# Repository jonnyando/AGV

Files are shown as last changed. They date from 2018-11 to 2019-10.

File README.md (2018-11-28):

# AGV

##Current Specs
- BLDC motor driver
- STM32F103C8 microcontroller
- LEDs on each phase's PWM output, so they will breath in sync with the speed of the motor
- Sense lines on all three phases, allowing sensorless operation
- UART connector
- SWD connector
- Vin up to 24V (need to double check voltage range on all parts)
- 3.3v linear reg (want to replace with switched)
- 3.3v rail indicator LED
- four quadrant operation (sw not yet implemented)

## TO DO
- add connection for rotary encoder
- add silkscreen indication for power input
- add bulk input capacitance
- get overall size down a little
- determine if parallel 'FETs are necessary for desired use cases.
- determine power handling capability (similar to above)

- usb port? depends on uC. Would need isolation probably
- isolated uart/i2c/spi port, for receiving commands from master/host
- add adc?

## Fixes:
- add power led on VBUS
- add led to EN_GATE pin to tell state
- increase drill size on stitching vias (currently unnecessarily small)
- fix/remove thermal relief on source pads for left most FETs
- add method to sense line voltages on each output phase, for back EMF sensing
- add fourth mounting hole
- increase package size where applicable (0402s are unnecessarily small in some places)
- do the capacitors on the back need to be there? maybe align them better at least
- improve fill polygon around C5 and C6
- align power leds more appropriately

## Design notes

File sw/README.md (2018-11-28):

# Software

to setup toolchain, download latest [arm-non-eabi-gcc package](https://developer.arm.com/open-source/gnu-toolchain/gnu-rm/downloads)

```bash
$ cd "${HOME}"/opt
$ tar xjf ~/Downloads/gcc-arm-none-eabi-7-2017-q4-major-linux.tar.bz2
$ chmod -R -w "${HOME}"/opt/gcc-arm-none-eabi-7-2017-q4-major
```

Update Makefile with __BINPATH__ reflecting the */opt/gcc-arm-none-eabi-7-2017-q4-major/bin/* folder created

vscode:
visual theme : `atom one dark`
icon theme : `material icon theme`

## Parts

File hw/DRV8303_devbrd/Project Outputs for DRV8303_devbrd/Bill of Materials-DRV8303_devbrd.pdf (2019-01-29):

Comment | Description | Designator | Footprint | LibRef | Quan tity
0.022uF | Non polarized capacitor | C1 | RESC0603(1608)_N | Capacitor | 1
1uF | Non polarized capacitor | C2, C3, C15, C24, C25 | RESC0603(1608)_N | Capacitor | 5
2.2uF | Non polarized capacitor | C4 | RESC0603(1608)_N | Capacitor | 1
4.7uF | Non polarized capacitor | C5 | RESC0603(1608)_N | Capacitor | 1
0.1uF | Non polarized capacitor | C6, C7, C8, C9, C10, C11, C21, C22, C23 | RESC0603(1608)_N | Capacitor | 9
2200pF | Non polarized capacitor | C12, C13 | RESC0603(1608)_N | Capacitor | 2
100nF | Non polarized capacitor | C14, C16, C17, C18, C20 | RESC0603(1608)_N | Capacitor | 5
10uF | Non polarized capacitor | C19 | RESC0603(1608)_N | Capacitor | 1
LED | | D1, D2, D3, D4, D5, D9 | 0603 | LED | 6
Diode_schottky | | D6, D7, D8 | SOD523 | Diode_schottky | 3
Mounting_hole | | M1, M2, M3, M4 | M3_drill | Mounting_hole | 4
Header 6 | Header, 6-Pin | P1 | HDR1X6 | Header 6 | 1
Header 4 | Header, 4-Pin | P2 | HDR1X4 | Header 4 | 1
ScrewTerm_2 | | P3 | ScrewTerm_2 | ScrewTerm_2 | 1
ScrewTerm_3 | | P4 | ScrewTerm_3 | ScrewTerm_3 | 1
FDMS7682 | | Q1, Q2, Q3, Q4, Q5, Q6, Q7, Q8, Q9, Q10, Q11, Q12 | PQFN8_5x6 | FDMS7682 | 12
0R | Resistor | R1 | RESC0603(1608)_N | Resistor | 1
10R | Resistor | R2, R3, R5, R6, R8, R9 | RESC0603(1608)_N | Resistor | 6
0.01R | Resistor | R4, R7 | RESC1206(3216)_M | Resistor | 2
56R | Resistor | R10, R11 | RESC0603(1608)_N | Resistor | 2
10KR | Resistor | R12, R13, R23, R24, R25 | RESC0603(1608)_N | Resistor | 5
1KR | Resistor | R14, R15, R16, R17, R18, R19, R29 | RESC0603(1608)_N | Resistor | 7
68KR | Resistor | R20, R21, R22 | RESC0603(1608)_N | Resistor | 3
DRV8303 | | U1 | HSSOP48 | DRV8303 | 1
STM32F103C8T6 | ARM Cortex-M3 32-bit MCU, 64 KB Flash, 20 KB Internal RAM, 37 I/Os, 48-pin LQFP, -40 to 85 degC, Tray | U2 | STM-LQFP48_N | STM32F103C8T 6 | 1
AZ1117EH | | U3 | SOT-223 | AZ1117EH | 1

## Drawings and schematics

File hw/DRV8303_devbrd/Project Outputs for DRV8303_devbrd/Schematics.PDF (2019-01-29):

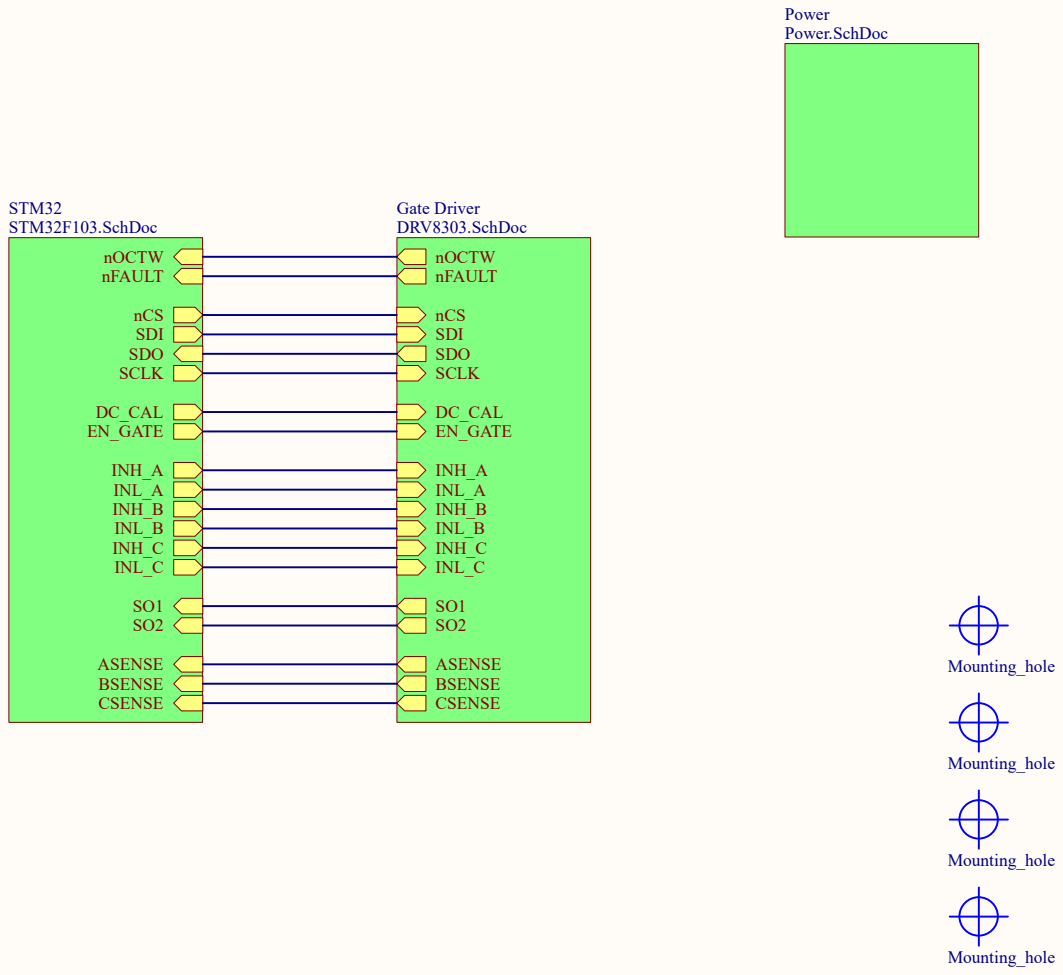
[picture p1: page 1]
Title; Size; Number; Revision; Date:; Sheet; File:; C:\Users\..\TopLevel.SchDoc; Drawn By:; nOCTW; nCS SDI; nFAULT; SDO SCLK; DC_CAL EN_GATE; INH_A INL_A INH_B INL_B INH_C INL_C; ASENSE BSENSE CSENSE; STM32 STM32F103.SchDoc; CSENSE; ASENSE BSENSE; Gate Driver DRV8303.SchDoc; Power Power.SchDoc; Mounting_hole

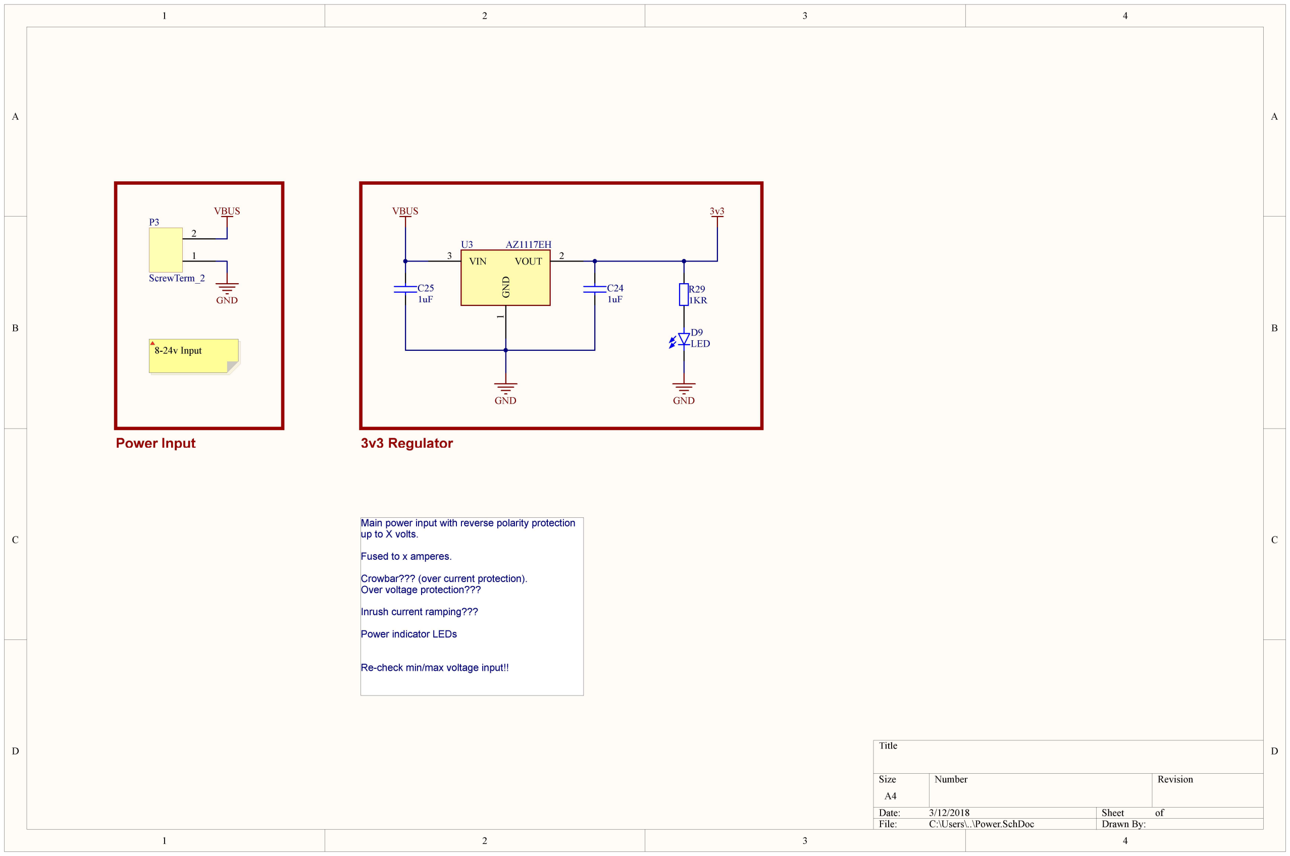
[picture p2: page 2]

D D

C C

B B

A A

Title

Size | Number | Revision
A4
File: | C:\Users\..\Power.SchDoc | Drawn By:

Main power input with reverse polarity protection up to X volts.

Fused to x amperes.

Crowbar??? (over current protection). Over voltage protection???

Inrush current ramping???

Power indicator LEDs

Re-check min/max voltage input!!

1

2

P3

ScrewTerm_2

VBUS

GND

3v3

GND

VBUS

C25
1uF

D9
LED

R29
1KR

GND

Power Input | 3v3 Regulator | GND

1

VOUT | 2 VIN 3
U3 | AZ1117EH

C24
1uF

8-24v Input

GND | 46 GND | 47 GND | 48 GND

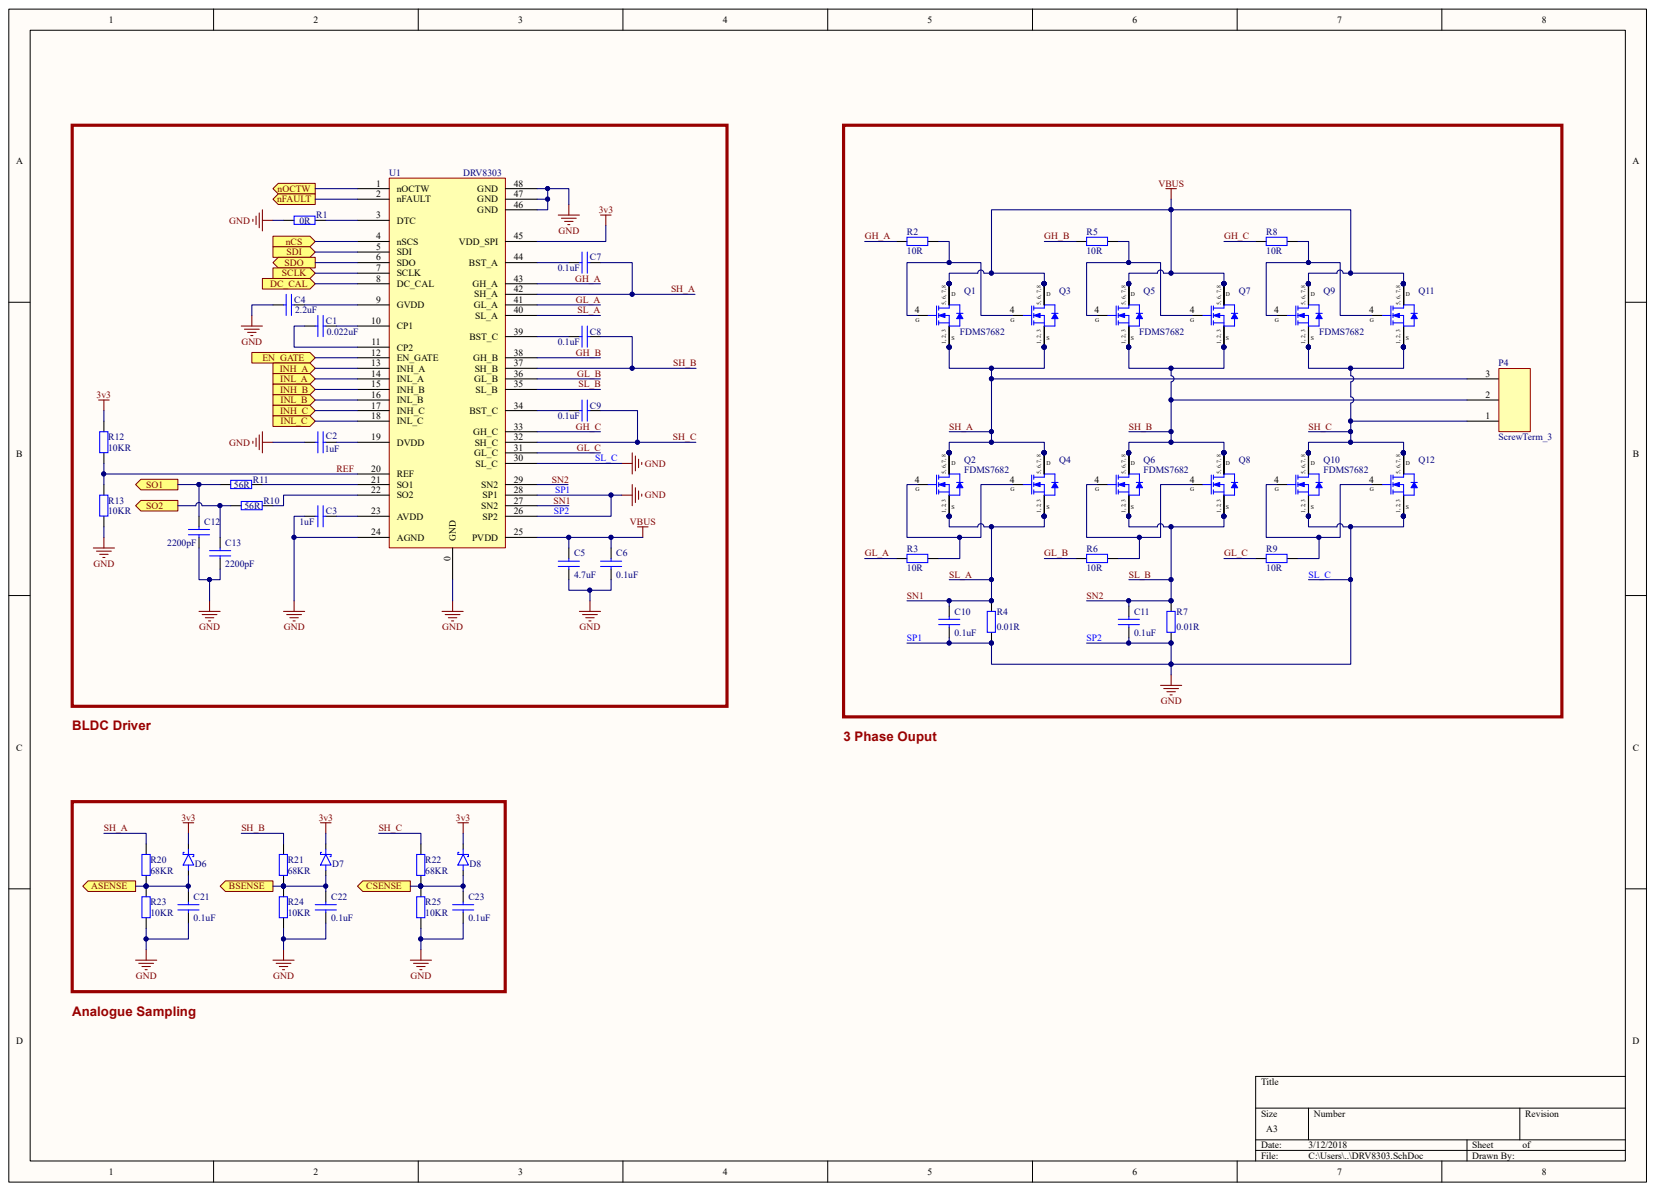
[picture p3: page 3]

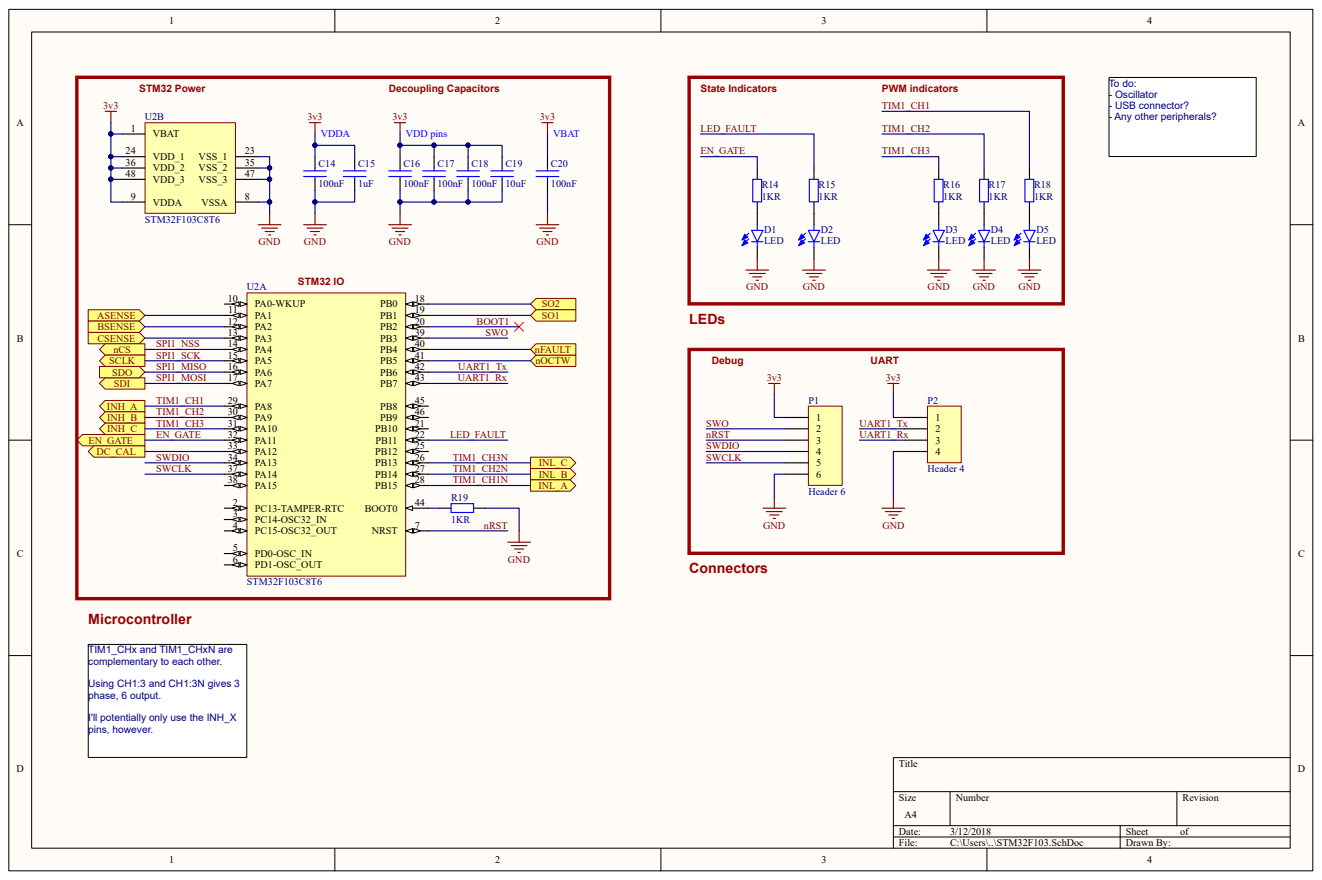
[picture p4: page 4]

TIM1_CHx and TIM1_CHxN are
complementary to each other.

I'll potentially only use the INH_X
pins, however.

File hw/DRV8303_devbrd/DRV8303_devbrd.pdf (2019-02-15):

Title; Size; Number; Revision; Date:; Sheet; File:; C:\Users\..\TopLevel.SchDoc; Drawn By:; nOCTW; nCS SDI; nFAULT; SDO SCLK; DC_CAL EN_GATE; INH_A INL_A INH_B INL_B INH_C INL_C; ASENSE BSENSE CSENSE; STM32 STM32F103.SchDoc; CSENSE; ASENSE BSENSE; Gate Driver DRV8303.SchDoc; Power Power.SchDoc; Mounting_hole

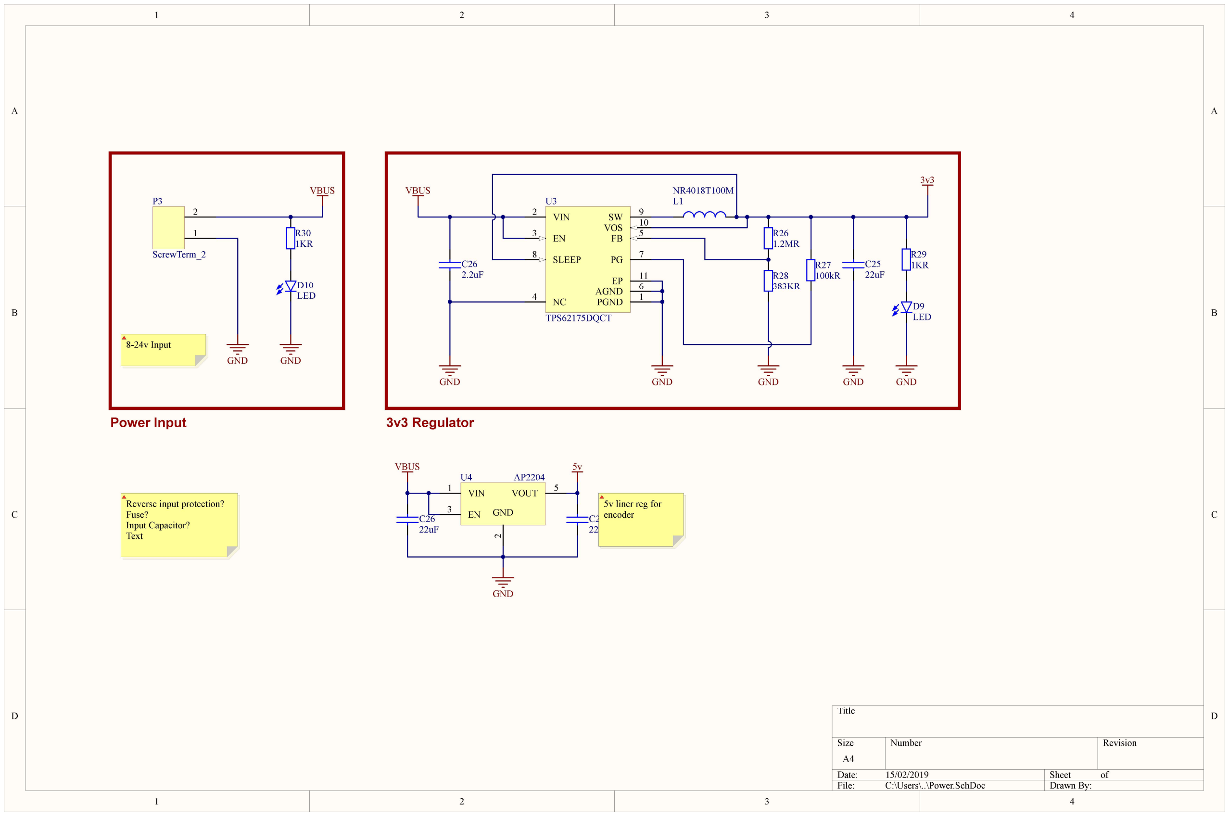
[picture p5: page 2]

D D

C C

B B

A A

Title

Size | Number | Revision
A4
File: | C:\Users\..\Power.SchDoc | Drawn By:

1

2

P3

ScrewTerm_2

VBUS

GND

D9
LED

R29
1KR

GND

Power Input | 3v3 Regulator
PGND | 1

VIN 2

EN 3

NC 4

FB | 5
AGND | 6
PG | 7 SLEEP 8
SW | 9
VOS | 10
EP | 11

U3

TPS62175DQCT

R26
1.2MR

R28
383KR

GND

C25
22uF

R27
100kR

GND

C26
2.2uF

VBUS

GND | GND

3v3

D10
LED

R30
1KR

GND

L1

NR4018T100M

GND

5v

VIN 1

GND2

EN 3

VOUT | 5
U4 | AP2204

VBUS

C26
22uF

C27
22uF

8-24v Input

Reverse input protection?
Fuse?
Input Capacitor?
Text

5v liner reg for
encoder

GND | 46 GND | 47 GND | 48 GND

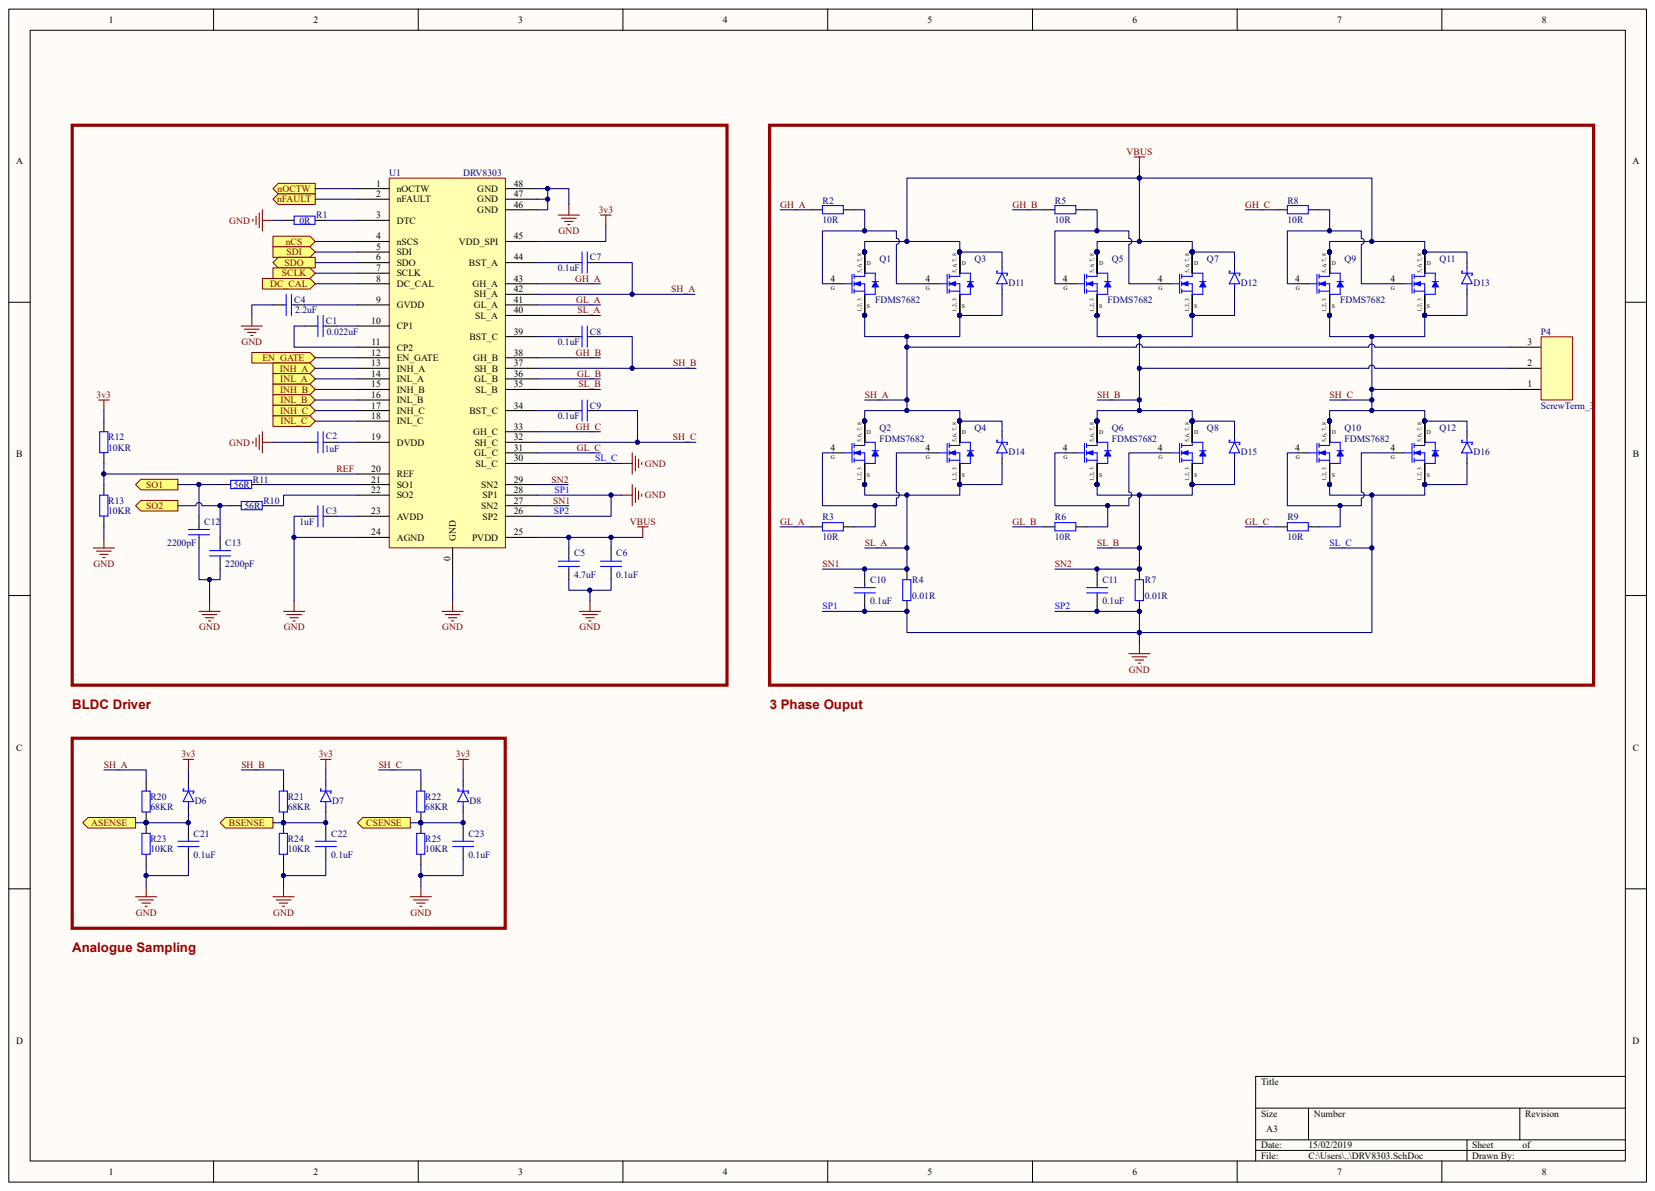
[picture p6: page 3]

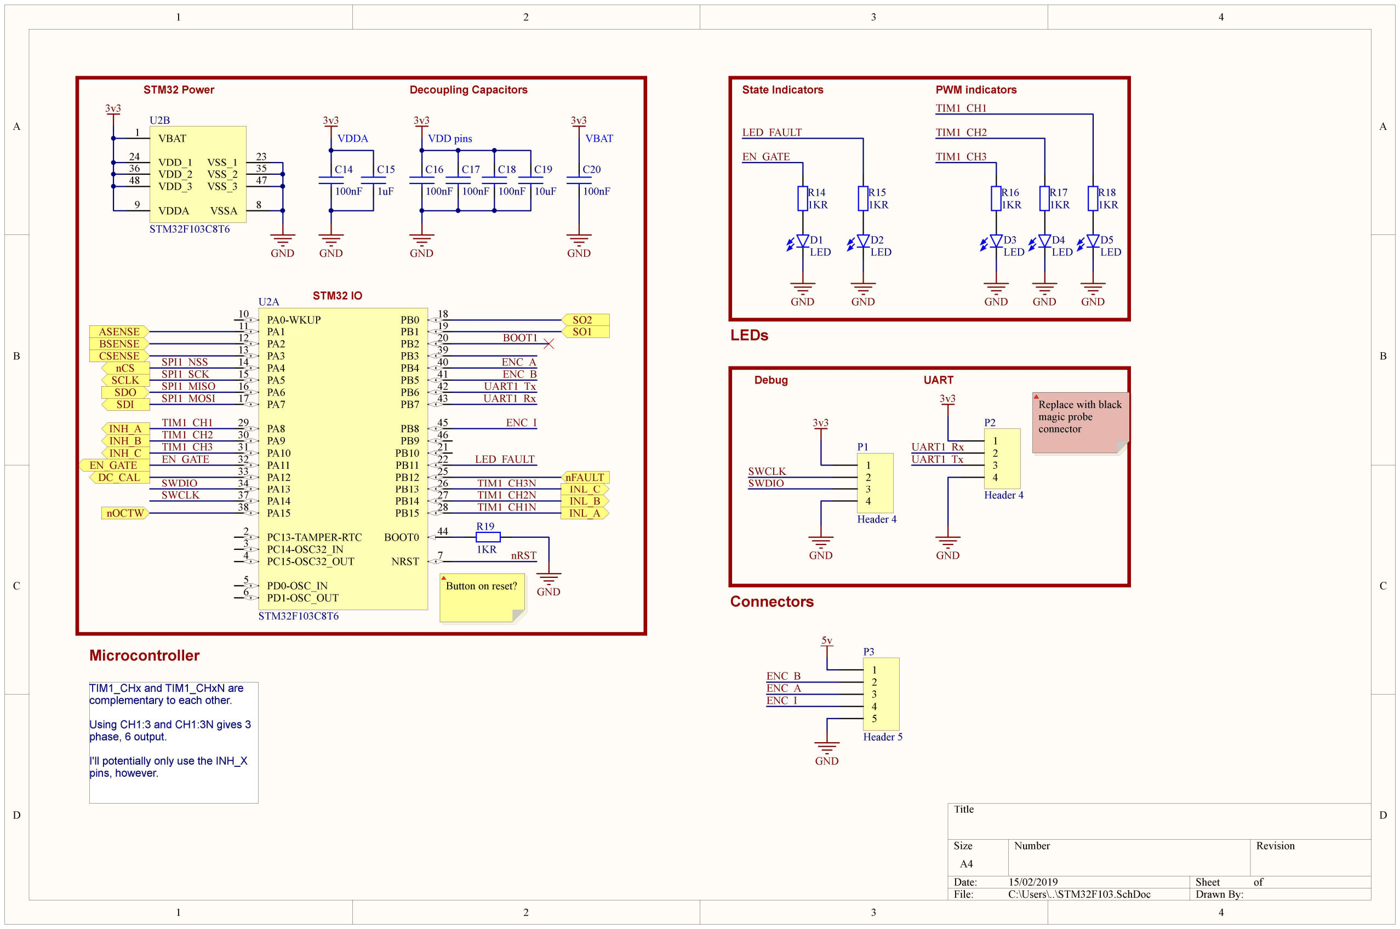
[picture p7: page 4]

D D

C C

B B

A A

Title

Size | Number | Revision
A4
File: | C:\Users\..\STM32F103.SchDoc | Drawn By:
BOOT0 | 44
NRST | 7

PA0-WKUP 10
PA1 11

PA10 31
PA11 32
PA12 33
PA13 34
PA14 37
PA15 38

PA2 12
PA3 13
PA4 14
PA5 15
PA6 16
PA7 17

PA8 29
PA9 30
PB0 | 18
PB1 | 19
PB10 | 21
PB11 | 22
PB12 | 25
PB13 | 26
PB14 | 27
PB15 | 28
PB2 | 20
PB3 | 39
PB4 | 40
PB5 | 41
PB6 | 42
PB7 | 43
PB8 | 45
PB9 | 46

PC13-TAMPER-RTC 2
PC14-OSC32_IN 3
PC15-OSC32_OUT 4

PD0-OSC_IN 5
PD1-OSC_OUT 6

U2A

STM32F103C8T6

VBAT 1

VDD_1 24
VDD_2 36
VDD_3 48

VDDA 9

VSS_1 | 23
VSS_2 | 35
VSS_3 | 47
VSSA | 8

U2B

STM32F103C8T6

EN_GATE

INH_A
INH_B

INL_B

INH_C

DC_CAL

nOCTW

nFAULT

GND

3v3

SWDIO

SWCLK

1
2
3
4

P2

Header 4

3v3

GND

UART1_Rx
UART1_Tx

R19

1KR

GND

nRST

SPI1_NSS
SPI1_SCK
SPI1_MISO
SPI1_MOSI

SWCLK

SWDIO

TIM1_CH1
TIM1_CH2
TIM1_CH3

TIM1_CH2N

TIM1_CHx and TIM1_CHxN are complementary to each other.

Using CH1:3 and CH1:3N gives 3 phase, 6 output.

I'll potentially only use the INH_X pins, however.

C16

100nF

C17

100nF

C18

100nF

C14

100nF

C15

1uF

C20

100nF

GND | GND | GND
3v3 | 3v3 | 3v3

C19

10uF

VDDA | VDD pins | VBAT
| Decoupling Capacitors
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
EN_GATE

EN_GATE

LED_FAULT

LED_FAULT

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
TIM1_CH1

TIM1_CH2

TIM1_CH3

STM32 Power

STM32 IO

## Microcontroller

## LEDs

State Indicators | PWM indicators

## Connectors

Debug | UART

ASENSE
BSENSE
CSENSE

UART1_Rx

UART1_Tx
SDI

nCS
SCLK
SDO

INL_C
INL_A TIM1_CH1N

TIM1_CH3N

SO2
SO1 BOOT1

1
2
3
4
5

P3

Header 5

ENC_A
ENC_B

ENC_I

5v

GND

ENC_A

ENC_B

ENC_I

1
2
3
4

P1

Header 4

Replace with black
magic probe
connector

Button on reset?

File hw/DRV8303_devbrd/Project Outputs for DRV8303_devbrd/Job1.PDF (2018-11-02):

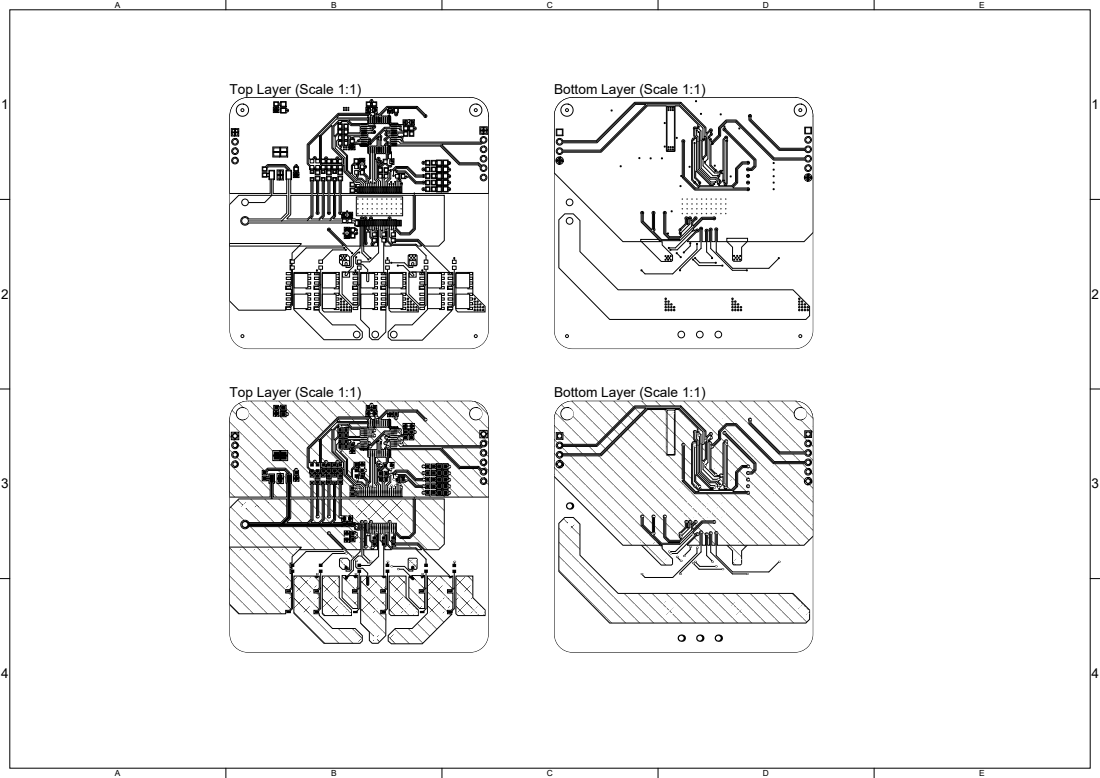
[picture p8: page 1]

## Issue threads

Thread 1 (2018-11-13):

Cannot communicate with DRV8303 over SPI

jonnyando, 2018-11-13:
Still debugging, but so far cannot see any data on the SDO line of the bus.

Current transmission looks like:
1. Lower chip select
2. transfer packet (R/W=1, address = 0010, data = 0)
3. Raise CS, delay 1mS, Lower CS
4. run SPI1_Tranceive(0x0000); to send zeroes and expecting to receive data back.

When running the above, only zeroes can be seen on the SDO line. No pulsing at all. Need to check IO configuration, but I expect it is correct.
Next things to check are baudrate, phase, and polarity of the clock.

jonnyando, 2018-11-14:
How it's initialised by ODrive firmware:
:   hspi3.Instance = SPI3;
   66:   hspi3.Init.Mode = SPI_MODE_MASTER;
   67:   hspi3.Init.Direction = SPI_DIRECTION_2LINES;
   68:   hspi3.Init.DataSize = SPI_DATASIZE_16BIT;
   69:   hspi3.Init.CLKPolarity = SPI_POLARITY_LOW;
   70:   hspi3.Init.CLKPhase = SPI_PHASE_2EDGE;
   71:   hspi3.Init.NSS = SPI_NSS_SOFT;
   72:   hspi3.Init.BaudRatePrescaler = SPI_BAUDRATEPRESCALER_16;
   73:   hspi3.Init.FirstBit = SPI_FIRSTBIT_MSB;
   74:   hspi3.Init.TIMode = SPI_TIMODE_DISABLE;
   75:   hspi3.Init.CRCCalculation = SPI_CRCCALCULATION_DISABLE;
   76:   hspi3.Init.CRCPolynomial = 10;

jonnyando, 2018-11-18:
Issue has been resolved.

There are two issues at play here - both hardware and software - with hardware being the biggest cause.

In the schematic, the placement of pins 23 and 24 are reversed, meaning AVDD is shorted directly to ground. Cutting the trace between that pin and the cap/via that bypasses it fixes the problem. The fix will be made in the schematic and new boards will be ordered soon.

For the software, I still haven't been able to figure out what hardware controlled NSS means, but I think it's only for Slave mode, so I've been using software controlled. The actual problem is the TX_empty flag gets raised before the transmission has completed on the hardware, so using that as a blocker to then raise chip select doesnt work and chip select get's raised about halfway through the transmission. I've implemented a NOP loop for the right amount of cycles, but will try to implement a proper delay function.

Closed 2018-11-18.

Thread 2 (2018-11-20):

PWM outputs are not connected to the correct pins

jonnyando, 2018-11-20:

jonnyando, 2018-12-27:
The pinout has been resolved in a new hardware revision, however PWM hasn't been implemented, so will no be determined if this is functioning until that time.

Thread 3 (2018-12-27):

inductive spiking kills 3.3v regulator

jonnyando, 2018-12-27:
On both boards with the 3v3 Reg, the regulator has shorted as soon as one of the motor phases is energised.

The output of the regulator is a direct short to ground. Checking the datasheet, the absolute maximum voltage input for the device is 16v. A spike of an extra 4v isn't crazy, so I believe when the motor phases' gates are raised, an inductive spike fries the regulator and kills the board.

I recommend implementing 2 fixes: input voltage clamping on the regulator and changing it to a switched-mode device.

One other "easier" alternative is to replace it with a 5v linear reg, which would presumably handle higher input voltages, but that's taking the easy way out.

jonnyando, 2019-05-20:
Added TVS in the latest hardware revision and have yet to see a similar failure.

Closed 2019-05-20.

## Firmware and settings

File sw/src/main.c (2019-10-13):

#include "main.h"

/* Private function prototypes -----------------------------------------------*/
void SystemClock_Config(void);

int __io_putchar(int ch)
{
    transmit_byte_uart(USART1, (uint8_t)ch);
    // ITM_SendChar(ch);
    return ch;
}

volatile uint32_t myTicks = 0;

void SysTick_Handler(void)
{
    myTicks++;
}

void DMA1_Channel1_IRQHandler(void){
    // pin_set(GPIOB, 11);
    if(DMA1->ISR & DMA_ISR_TEIF1){
        printf("DMA error\n");
        DMA1->IFCR |= (DMA_IFCR_CGIF1 | DMA_IFCR_CTEIF1);
    } else if(DMA1->ISR & DMA_ISR_HTIF1){
        // printf("DMA half transfer\n");
        DMA1->IFCR |= (DMA_IFCR_CGIF1 | DMA_IFCR_CHTIF1);
    } else if(DMA1->ISR & DMA_ISR_TCIF1){
        // printf("DMA transfer complete\n");
        DMA1->IFCR |= (DMA_IFCR_CGIF1 | DMA_IFCR_CTCIF1);
    }else if(DMA1->ISR & DMA_ISR_GIF1){
        // printf("DMA global interrupt\n");
        DMA1->IFCR |= DMA_IFCR_CGIF1;
    }
}

void ADC1_2_IRQHandler(void){
    // pin_set(GPIOB, 11);
    // blink_fault();
    // printf("ADC interrupt\n");
}

void HardFault_Handler(void){
    pin_set(GPIOB, 11);
}
void BusFault_Handler(void){
    pin_set(GPIOB, 11);
}
void UsageFault_Handler(void){
    pin_set(GPIOB, 11);
}

void myDelay(uint32_t mS){
    myTicks = 0;
    while(myTicks<mS);
}

uint16_t ADC_samples[10];

void blink_fault(void){
    pin_reset(GPIOB, 11);
    myDelay(50);
    pin_set(GPIOB, 11);
    myDelay(50);
    pin_reset(GPIOB, 11);
    myDelay(50);
    pin_set(GPIOB, 11);
}

int main(void)
{   
    // SystemInit();
    SystemClock_Config();



    pin_reset(GPIOB, 11);
    myDelay(50);
    pin_set(GPIOB, 11);
    myDelay(50);
    pin_reset(GPIOB, 11);
    myDelay(50);
    pin_set(GPIOB, 11);

    watchdog_set_prescaler(32);
    watchdog_set_reload_reg(0xfff);
    watchdog_start();

    GPIO_Init();
    UART_Init(USART1);
    UART_pin_Remap(USART1, 1);
    printf("uart1 initialized\n");
    printf("gpio initialized\n");
    SPI_Init(SPI1);             printf("SPI1 initialized\n");
    
    if(RCC->CSR & RCC_CSR_IWDGRSTF){
        printf("\nIWDG reset detected\n");
    }
    printf("mem adress: ADC1->DR=%d\n",&(ADC1->DR));
    

    NVIC_SetPriority(HardFault_IRQn, 0);
    NVIC_EnableIRQ(HardFault_IRQn);
    NVIC_SetPriority(BusFault_IRQn, 0);
    NVIC_EnableIRQ(BusFault_IRQn);
    NVIC_SetPriority(UsageFault_IRQn, 0);
    NVIC_EnableIRQ(UsageFault_IRQn);

    // printf("RCC->CR\t\t");          print_reg(RCC->CR,     32);

    RCC->AHBENR |= RCC_AHBENR_DMA1EN;
    DMA1_Channel1->CPAR = (uint32_t)&(ADC1->DR);
    DMA1_Channel1->CMAR = (uint32_t)ADC_samples;
    DMA1_Channel1->CNDTR = 5;
    DMA1_Channel1->CCR &= ~(DMA_CCR_PL_0 | DMA_CCR_PL_1);
    // DMA1_Channel1->CNDTR = (sizeof(ADC_samples)/sizeof(ADC_samples[0]));
    // memory icnrement
    // circular mode
    // set peripheral and memory sizes to 16b
    DMA1_Channel1->CCR |= DMA_CCR_MINC | DMA_CCR_CIRC 
                        | DMA_CCR_PSIZE_0 | DMA_CCR_MSIZE_0
                        | DMA_CCR_TEIE | DMA_CCR_TCIE | DMA_CCR_HTIE;
    // DMA1_Channel1->CCR &= ~(DMA_CCR_HTIE);
    DMA1_Channel1->CCR |= DMA_CCR_EN;
    
    // enable
    myDelay(500);

    printf("DMA1 Channel1 initialised\n");
    
    ADC1_Init();    printf("ADC1 initialized\n");

    ADC1->CR1 |= ADC_CR1_EOCIE;
    ADC1->CR2 |= ADC_CR2_CONT;
    ADC1->CR2 |= ADC_CR2_ADON;
    myDelay(10);
    ADC1->CR2 |= (ADC_CR2_RSTCAL);
    ADC1->CR2 |= (ADC_CR2_CAL);
    printf("adc on, calibrating...\n");
    while((ADC1->CR2) & (ADC_CR2_CAL)){
        // myDelay(1);
        ;
    }
    ADC1->CR2 |= ADC_CR2_ADON;


    myDelay(10);
    // print_reg(ADC1->CR2, 32);
    printf("adc on and calibrated\n");
    myDelay(10);
    myDelay(500);
    

    TIM1_Init();                printf("tim1 initialized\n");
    pin_reset(DC_CAL_Port, DC_CAL_Pin);
    printf("DC_CAL set LOW (off)\n");
    myDelay(10);
    uint16_t tx;
    uint16_t rx;

    drv8303_TypeDef drv;
    drv8303_Init(&drv, SPI1);
    drv_update(&drv);

    // sets OC_ADJ_SET to 24 (Vds = 1.043v)
    // Disable OCP
    // sets drv to 3-PWM mode
    // uint16_t set_reg = 0b01000000000 | 0b00000110000 | 0b00000001000;
    // uint16_t set_reg = (CR1_OC_ADJ_SET_24 | CR1_OCP_MODE_DISABLED | CR1_PWM_MODE_3);
    uint16_t set_reg = (CR1_OC_ADJ_SET_7 | CR1_PWM_MODE_3);
    pin_set(EN_GATE_Port, EN_GATE_Pin);
    myDelay(100);
    drv_write(&drv, DRV_CTRL_1, set_reg);
    printf("\nEnabled DRV8303\n");

    // myDelay(10);
    myDelay(500);
    printf("transmitting to drv\n");
    rx = drv_read(&drv, DRV_STATUS_1);
    printf("Status register 1\t");   print_reg(rx, 16);
    rx = drv_read(&drv, DRV_STATUS_2);
    printf("Status register 2\t");   print_reg(rx, 16);
    rx = drv_read(&drv, DRV_CTRL_1);
    printf("Control register 1\t");  print_reg(rx, 16);
    rx = drv_read(&drv, DRV_CTRL_2);
    printf("Control register 2\t");  print_reg(rx, 16);
    myDelay(10);
    // rx = drv_read(0x03);
    // printf("Control register 2\t");  print_reg(rx, 16);
    // myDelay(10);

    printf("\n");
    uint16_t t_del = 50;
    TIM1_enable();


    uint32_t angle_a = 0;
    uint32_t angle_b = 0;
    uint32_t angle_c = 0;
    uint32_t max_duty_cycle = 7500;
    uint16_t duty_cycle_a;
    uint16_t duty_cycle_b;
    uint16_t duty_cycle_c;
    uint16_t angle_step = 30;
    
    // uint8_t tc[3] = "abc";
    // transmit_byte_uart1(*tc);
    // transmit_byte_uart1('\n');
    // transmit_uart(USART1, tc, 3);

    drv_update(&drv);
    
    // drv_write(&drv, DRV_CTRL_1, set_reg);
    watchdog_reload();
    printf("Interrupts enabled\n");

    
    NVIC_SetPriority(DMA1_Channel1_IRQn, 1);
    NVIC_EnableIRQ(DMA1_Channel1_IRQn);
    NVIC_SetPriority(ADC1_IRQn, 2);
    NVIC_EnableIRQ(ADC1_IRQn);
    printf("while(1)\n");
    while (1){
        // while(1){
        //     ;
        // }
        // myDelay(200);
        // printf("beep..\n");
        // fflush(stdout);
        // ASENSE, BSENSE, CSENSE, A_CURR, B_CURR
        // for(int i = 0; i < 4; i++){
        //     printf("%d, ", ADC_samples[i]);
        // }
        // printf("%d\n", ADC_samples[4]);
        
        // if (DMA1->ISR & DMA_ISR_TEIF1){
        //     printf("DMA1 error interrupt\n");
        //     DMA1->IFCR |= DMA_IFCR_CTEIF1;
        //     DMA1->IFCR |= DMA_IFCR_CGIF1;
        // }
        // if (DMA1->ISR & DMA_ISR_HTIF1){
        //     printf("DMA1 half transfer interrupt\n");
        //     DMA1->IFCR |= DMA_IFCR_CHTIF1;
        //     DMA1->IFCR |= DMA_IFCR_CGIF1;
        // }
        // if (DMA1->ISR & DMA_ISR_TCIF1){
        //     printf("DMA1 transfer complete interrupt\n");
        //     DMA1->IFCR |= DMA_IFCR_CTCIF1;
        //     DMA1->IFCR |= DMA_IFCR_CGIF1;
        // }

        myDelay(10);

        // if(!pin_read(nOCTW_Port, nOCTW_Pin)){
        //     printf("nOCTW is LOW\n");
        //     pin_set(LED_FAULT_Port, LED_FAULT_Pin);
        // } else if(!pin_read(LED_FAULT_Port, nFAULT_Pin)){
        //     printf("nFAULT is LOW\n");
        //     pin_set(LED_FAULT_Port, LED_FAULT_Pin);
        // } else {
        //     pin_reset(LED_FAULT_Port, LED_FAULT_Pin);
        // }

        pin_reset(LED_FAULT_Port, LED_FAULT_Pin);

        angle_b = angle_a + 120;
        angle_c = angle_a + 240;

        duty_cycle_a = ((sin(angle_a * (PI/180))+1)/2)*max_duty_cycle;
        duty_cycle_b = ((sin(angle_b * (PI/180))+1)/2)*max_duty_cycle;
        duty_cycle_c = ((sin(angle_c * (PI/180))+1)/2)*max_duty_cycle;
        // global_angle = fmod(global_angle, 360);
        angle_a =  angle_a + angle_step;
        angle_a %= 360;
        // printf("%d, %d, %d, %d\n", (uint32_t)duty_cycle_a, (uint32_t)duty_cycle_b, (uint32_t)duty_cycle_c, angle_a);

        TIM1->CCR1  = duty_cycle_a;
        TIM1->CCR2  = duty_cycle_b;
        TIM1->CCR3  = duty_cycle_c;

        watchdog_reload();
    }



}

/**@brief System Clock Configuration*/
void SystemClock_Config(void)
{
    
    RCC->CR |= (1 << 0);          // HSI enable
    while(!(RCC->CR & (1<<1)));  // wait for HSI to stabilise
    // calibrate
    // RCC->CFGR &= ~(0b1110 << 18);  // PLLMUL = x16
    RCC->CFGR = (RCC->CFGR & (~RCC_CFGR_PLLMULL16))| RCC_CFGR_PLLMULL16;  // PLLMUL = x16
    RCC->CFGR &= ~RCC_CFGR_PLLSRC;       // PLLSOURCE = HSI/2
    RCC->CR |= (1 << 24);         // PLL enable
    while(!(RCC->CR & (1<<25))); // wait for PLL to stabilise

     // increase FLASH latency before setting SYSCLK > 24MHz
    FLASH->ACR = (FLASH->ACR & (~FLASH_ACR_LATENCY)) | FLASH_ACR_LATENCY_2;

    RCC->CFGR |= RCC_CFGR_HPRE_DIV1; // Set AHB prescaler to SYSLCK/1
    RCC->CFGR = (RCC->CFGR & (~RCC_CFGR_SW_Msk)) | RCC_CFGR_SW_PLL;    // Set SYSCLCK to PLL
    while(!((RCC->CR & RCC_CR_PLLRDY) && (RCC->CR & RCC_CR_HSIRDY)));
    while((RCC->CFGR & RCC_CFGR_SWS) != RCC_CFGR_SWS_PLL);

    RCC->CFGR = (RCC->CFGR & (~RCC_CFGR_PPRE1_Msk)) | RCC_CFGR_PPRE1_DIV2;  // APB1 = HCLK/2
    RCC->CFGR = (RCC->CFGR & (~RCC_CFGR_PPRE2_Msk)) | RCC_CFGR_PPRE2_DIV1;  // APB2 = HCLK/1

    // SystemCoreClock = 64000000;
    SystemCoreClockUpdate();
    
    /*Configure the Systick interrupt time*/
    SysTick_Config(64000);
    NVIC_SetPriority(SysTick_IRQn, 0);

}

static void GPIO_Init(void)
{
    /* GPIO Ports Clock Enable */
    RCC->APB2ENR |= RCC_APB2ENR_AFIOEN; // enable AFIO
    RCC->APB2ENR |= RCC_APB2ENR_IOPAEN; // enable GPIOA
    RCC->APB2ENR |= RCC_APB2ENR_IOPBEN; // enable GPIOB
    RCC->APB2ENR |= RCC_APB2ENR_IOPCEN; // enable GPIOC
    RCC->APB2ENR |= RCC_APB2ENR_IOPDEN; // enable GPIOD

    pin_mode(     nOCTW_Port, nOCTW_Pin, GPIO_IN_PULL);
    pin_pullmode( nOCTW_Port, nOCTW_Pin, GPIO_PULLUP);
    pin_mode(     nFAULT_Port, nFAULT_Pin, GPIO_IN_PULL);
    pin_pullmode( nFAULT_Port, nFAULT_Pin, GPIO_PULLUP);
    
    pin_mode(DC_CAL_Port,  DC_CAL_Pin,  GPIO_OUT_PP);
    pin_mode(EN_GATE_Port, EN_GATE_Pin, GPIO_OUT_PP);
    pin_mode(INH_A_Port,   INH_A_Pin,   GPIO_AF_PP);
    pin_mode(INH_B_Port,   INH_B_Pin,   GPIO_AF_PP);
    pin_mode(INH_C_Port,   INH_C_Pin,   GPIO_AF_PP);
    pin_mode(INL_A_Port,   INL_A_Pin,   GPIO_AF_PP);
    pin_mode(INL_B_Port,   INL_B_Pin,   GPIO_AF_PP);
    pin_mode(INL_C_Port,   INL_C_Pin,   GPIO_AF_PP);
    pin_mode(LED_FAULT_Port, LED_FAULT_Pin, GPIO_OUT_PP);

    // SPI Pin setup
    pin_mode(SPI_PORT, SPI_Pin_NSS, GPIO_OUT_PP); // NSS
    pin_mode(SPI_PORT, SPI_Pin_SCK, GPIO_AF_PP);  // SCK,
    pin_mode(SPI_PORT, SPI_Pin_MISO, GPIO_IN_FL);  // MISO
    pin_mode(SPI_PORT, SPI_Pin_MOSI, GPIO_AF_PP);  // MOSI

    // setup GPIO pins for USART1
    pin_mode(USART1_PORT, USART_Pin_RX, GPIO_IN_FL); // RX PB7
    pin_mode(USART1_PORT, USART_Pin_TX, GPIO_AF_PP); // TX PB6

    // setup GPIO pins for ADC1
    pin_mode(ASENSE_Port, ASENSE_Pin, GPIO_IN_AN);
    pin_mode(BSENSE_Port, BSENSE_Pin, GPIO_IN_AN);
    pin_mode(CSENSE_Port, CSENSE_Pin, GPIO_IN_AN);
    pin_mode(SO1_Port,    SO1_Pin,    GPIO_IN_AN);
    pin_mode(SO2_Port,    SO2_Pin,    GPIO_IN_AN);
}

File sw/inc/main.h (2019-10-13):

#ifndef __MAIN_H__
#define __MAIN_H__

/* Includes ------------------------------------------------------------------*/

// #include "syscalls.h"
// #include "stm32f1xx_hal.h"
#ifndef STM32F103xB
    #define STM32F103xB
#endif
#include "stm32f1xx.h"
#include "spi.h"
#include "uart.h"
#include "gpio.h"
#include "tim.h"
#include <stdio.h>
#include <math.h>
#include "drv8303.h"
#include "adc.h"
#include "dma.h"
#include "iwdg.h"

/* Private define ------------------------------------------------------------*/
#define PI 3.14159265358979323846264


#define nOCTW_Pin       15 // A
#define nOCTW_Port      GPIOA
#define nFAULT_Pin      12 // B
#define nFAULT_Port     GPIOB
#define DC_CAL_Pin      12     // A 
#define DC_CAL_Port     GPIOA
#define EN_GATE_Pin     11     // A
#define EN_GATE_Port    GPIOA
#define INH_A_Pin       8      // A
#define INH_B_Pin       9      // A
#define INH_C_Pin       10     // A
#define INH_A_Port      GPIOA
#define INH_B_Port      GPIOA
#define INH_C_Port      GPIOA
#define INL_A_Pin       13     // B
#define INL_B_Pin       14     // B
#define INL_C_Pin       15     // B
#define INL_A_Port      GPIOB
#define INL_B_Port      GPIOB
#define INL_C_Port      GPIOB
#define LED_FAULT_Pin   11     // B
#define LED_FAULT_Port  GPIOB
#define ENC_I           8      // B
#define ENC_A           4      // B
#define ENC_B           5      // B
#define ASENSE_Pin      1      // A
#define BSENSE_Pin      2      // A
#define CSENSE_Pin      3      // A
#define ASENSE_Port     GPIOA
#define BSENSE_Port     GPIOA
#define CSENSE_Port     GPIOA
#define SO1_Pin         1      // B
#define SO2_Pin         0      // B
#define SO1_Port        GPIOB
#define SO2_Port        GPIOB
/* SPI Pins */
#define SPI_PORT        GPIOA
#define SPI_Pin_NSS     4
#define SPI_Pin_SCK     5
#define SPI_Pin_MISO    6
#define SPI_Pin_MOSI    7
/* USART1 Pins */
#define USART1_PORT     GPIOB
#define USART_Pin_TX    6
#define USART_Pin_RX    7


// #define B1_Pin GPIO_PIN_13
// #define B1_GPIO_Port GPIOC
// #define B1_EXTI_IRQn EXTI15_10_IRQn
// #define USART_TX_Pin GPIO_PIN_2
// #define USART_TX_GPIO_Port GPIOA
// #define USART_RX_Pin GPIO_PIN_3
// #define USART_RX_GPIO_Port GPIOA
// #define SWO_Pin GPIO_PIN_3
// #define SWO_GPIO_Port GPIOB



#endif /* __MAIN_H__ */

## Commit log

2018-03-30 migrated project to github
    [DRV8303.sch, motor_driver.kicad_pcb, motor_driver.sch]
2018-04-04 Finished layout and generated gerbers
    [motor_driver-B.Cu.gbl, motor_driver-B.Mask.gbs, motor_driver-B.SilkS.gbo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]
2018-06-03 moved hardware and software into discrete folders. Added software template
    [DRV8303.sch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]
2018-06-03 began spi integration
2018-06-16 SPI is now working. Wrote a few debug functions using HAL_UART3
2018-06-17 Uart1-3, printf, spi all working
2018-11-02 re organised file structure, and updated hardware files with new Altium version
    [DRV8303.SchDoc, DRV8303.sch, DRV8303_devbrd.PrjPCB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]
2018-11-19 functioning SPI comms
2018-11-21 fixed grounding path to power input connector. fixed pin issue on AVDD in drv8303
    [Bill of Materials-DRV8303_devbrd.xlsx, DRV8303.SchDoc, DRV8303_devbrd.PrjPCB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]
2018-11-28 swapped TIM1_CHx to correct pins. Moved UART to alt pins, and swapped a few nets around to simplify routing. Gerbers of this commit submitted for fab
    [STM32F103.SchDoc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]
2018-11-28 began switch over to vscode
2018-11-28 renamed some UART functions
2018-11-29 created drv_write() and set a reg for 3-PWM mode control
2019-01-29 begun modifications for Rev C - currently unworking state
    [DRV8303.SchDoc, DRV8303_devbrd.PrjPCB]
2019-02-02 added SMPS and flyback diode
    [DRV8303.SchDoc, Power.SchDoc, STM32F103.SchDoc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]
2019-02-03 Added encoder connetions and reworked connectors
    [DRV8303.SchDoc, Power.SchDoc, STM32F103.SchDoc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]
2019-02-08 updated power schematic
    [Power.SchDoc, drv8303_brd.PcbDoc]
2019-02-09 reworked gpio manipulation and changed name of uart lib
    [main.c]
2019-02-15 updated PCB for new revision. Gerbers ordered
    [Power.SchDoc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]
2019-05-19 SPI working for real
2019-07-17 cleaned up pin assignment in uart driver
2019-09-03 updated drv driver to use an object handle
2019-09-03 uart driver now peripheral number agnostic
2019-09-03 cleaned up spi driver
2019-10-13 interrupts for debugging. WIP
